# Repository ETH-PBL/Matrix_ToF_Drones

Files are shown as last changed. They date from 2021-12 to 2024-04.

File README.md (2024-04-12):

<!--
*** Template source: https://github.com/othneildrew/Best-README-Template/blob/master/README.md
-->

<!-- PROJECT SHIELDS -->
<!--
*** I'm using markdown "reference style" links for readability.
*** Reference links are enclosed in brackets [ ] instead of parentheses ( ).
*** See the bottom of this document for the declaration of the reference variables
*** for contributors-url, forks-url, etc. This is an optional, concise syntax you may use.
*** https://www.markdownguide.org/basic-syntax/#reference-style-links
-->
[][contributors-url]
[][forks-url]
[][stars-url]
[][issues-url]
[][license-url]

<!-- PROJECT LOGO -->
<br />
<p align="center">
  <a href="https://youtu.be/FyipTqjBGuM">
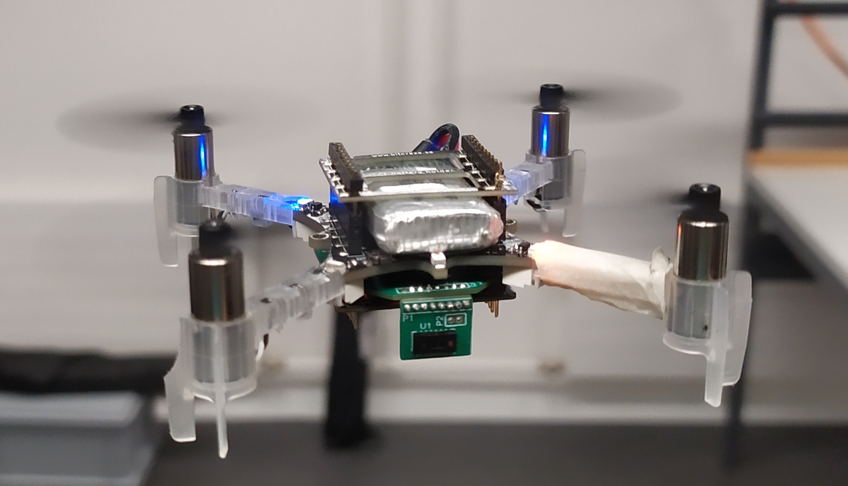
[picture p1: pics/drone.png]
    
  </a>

  <h3 align="center">Matrix_ToF_Drones</h3>

  <p align="center">
    Indoor Navigation System Based on Multi-Pixel Time-of-Flight Imaging for Nano-Drone Applications
    <br />
    <a href="https://github.com/ETH-PBL/Matrix_ToF_Drones"><strong>Explore the docs »</strong></a>
    <br />
    <br />
    <a href="https://youtu.be/FyipTqjBGuM">View Demo</a>
    ·
    <a href="https://github.com/ETH-PBL/Matrix_ToF_Drones/issues">Report Bug</a>
    ·
    <a href="https://github.com/ETH-PBL/Matrix_ToF_Drones/issues">Request Feature</a>
  </p>
</p>

<!-- TABLE OF CONTENTS -->
## Table of Contents

* [About the Project](#about-the-project)
* [Hardware](#hardware)
  * [Components](#hardware)
  * [PCB](#pcb) 
* [Dataset](#dataset)
  * [Dataset Visualizer](#visualizer)
* [Getting Started](#getting-started)
  * [Software](#software)

<!-- ABOUT THE PROJECT -->
## About The Project

Unmanned aerial vehicles (UAVs) have recently attracted the industry's attention due to their numerous civilian and potential commercial applications.
A promising UAV sub-class includes nano and micro UAVs, characterized by centimeter size, few grams of payload and extremely limited on-board computational resources. 
Those features pose major challenges to enable autonomous navigation or even more basic relevant sub-tasks, such as reliable obstacle avoidance. This project exploits a multi-zone Time of Flight (ToF) sensor to enable autonomous navigation and obstacle avoidance with a low lower computational load than most common visual-based solutions. 

### Videos and Demos
* [PBL Event: catch me if you can][video1_url]
* [Towards Reliable Obstacle Avoidance for Nano-UAVs][video2_url]
* [Enabling Obstacle Avoidance for Nano-UAVs with a multi-zone depth sensor and a model-free policy][video3_url]

## Hardware

The matrix ToF sensor, and thus this project aims to characterize and in-field evaluate the sensors <a href="https://www.st.com/resource/en/datasheet/vl53l5cx.pdf">VL53L5CX</a> from STMicroelectronics using a nano-drone platform. This project exploits a commercial nano-UAV platform, the Crazyflie 2.1 from bitcraze, together with a custom PCB designed to support two 8x8 ToF sensors. The following sections describe in detail the overall framework and the hardware setup.

### Components
The <a href="https://www.st.com/resource/en/datasheet/vl53l5cx.pdf">VL53L5CX</a> is a ToF multizone ranging sensor produced by STMicroelectronics. 
It integrates a single-photon avalanche diode (SPAD) array, physical infrared filters, and diffractive optical elements (DOE) to achieve a millimeter accuracy in various ambient lighting conditions with a wide range of cover glass materials. The working range spans between 2 cm and 4 meters, but above 2 m, the overall ranging precision degrades to 11% of the absolute distance. The most important feature of the VL53L5CX is the multizone capability, which can be configured as an 8x8 or 4x4 matrix. 
Listed below is the list of key components for our integrated deck targetted for the Crazyflie 2.1 platform: 

* [VL53L5CX][VL53L5CX_url],       ToF multizone ranging sensor
* [TPS62233][tps62233_url],       3-MHz Ultra Small Step-Down Converter
* [TCA6408A][tca6408a_url],       Low-Voltage 8-Bit I2C and SMBus I/O Expander

### PCB 
The matrix ToF printed circuit board (PCB) is built of 2 Layers with a total board thickness of only 0.43mm. Further information about the PCB can be found here:

File                                  | Content
--------------------------------------|--------
[Deck_schematics.pdf]                 | Schematics of the deck that supports 2 VL53L5CX.  
[Deck_PCB_3D.pdf]                     | Layout 3D view with details of components and nets.
[Deck_BOM.xlsx]			      | Bill of material for the Deck PCB.
[Sensor_Board_schematics.pdf]         | Schematic of the lateral PCB that holds one VL53L5CX.
[Sensor_Board_PCB_3D.pdf]             | Layout 3D view with details of components and nets.
[Sensor_Board_BOM.xlsx]               | Bill of material for the sensor board.
[Final_Assembly_3D.pdf]               | Assembly of one Deck PCB with two sensor board PCBs, front-facing and back-facing directions. 

The preview of the assembly, with details of logical connections, can be found here:

<p align="center">
<a href="https://github.com/ETH-PBL/Matrix_ToF_Drones/Hardware/TofDeck/Deck_3D.pdf">
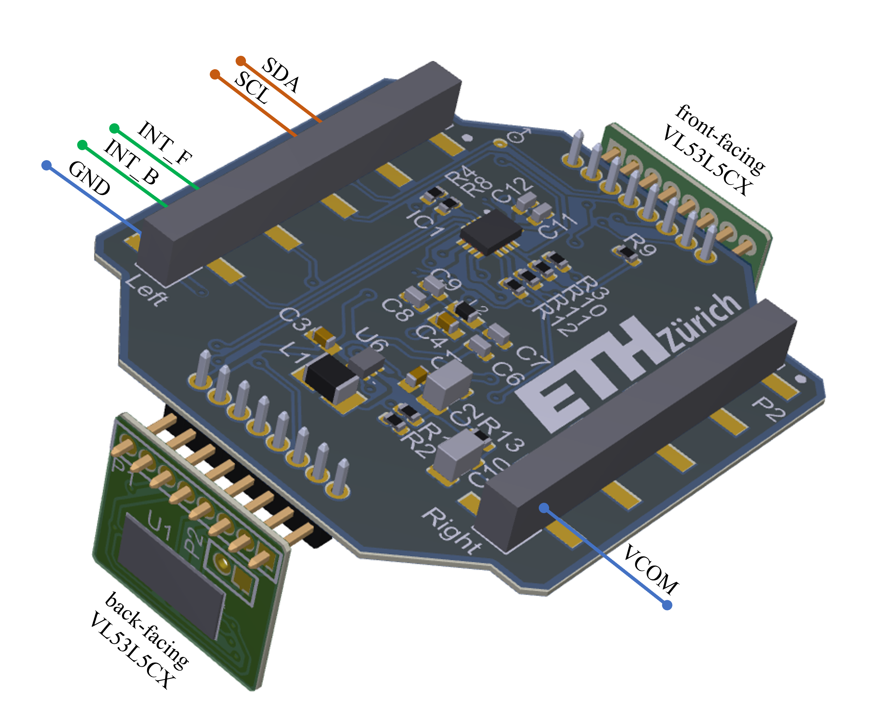
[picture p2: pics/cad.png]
    
</a>
</p>

## Dataset

Tests were performed in controlled and open spaces, with the support of a motion capture system (mocap) Vicon Vero 2.2 at a rate of 50 Hz. A human pilot manually steered the Crazyflie. Initially, the dataset was used to develop and test the obstacle avoidance algorithm. However, other researchers can also use it to improve our system by integrating the multi-zone ToF data with processed information from a CNN and the grayscale camera or by applying a more general DNN algorithm to enhance on-board intelligence. 
We collected (a) internal state estimation (attitude, velocity, position) of the Crazyflie, (b) multi-zone ToF array in 8x8 pixel configuration, (c) camera images (QVGA greyscale), (d) Vicon data (attitude, position) in a time series format with millisecond accuracy. The dataset consists of three main groups: object approach moving the drone on a single axis, yaw rotations around the Z-axis, and a general-purpose set of flying tests approaching various obstacles and narrow holes. The first group, named Linear Movements, consists of 10 recordings of flights with (a), (b), (c), and (d) data, approaching a wood panel at different speeds and stopping and flying back always on the same axis, rotations and altitude variations are disabled. The total test time is 216 seconds with an average of 22 seconds per acquisition. The next group, Yaw Rotations, consists of 3 recordings with (a), (b), (c), and (d) data, rotating on a single axis (yaw) at 1 meter from an obstacle. Recorded data reach a total of 94 seconds. The third and final group, named Obstacle Avoidance, is composed of 30 recordings with a mixed combination of (a), (b), (c), (d) - 14 acquisitions - and (a), (b), (c) - 16 acquisitions. In total, for the third group, 17 minutes of flight maneuvers are present in the Flight DataSet folder, with an average of 35 seconds per acquisition. 

The list of experiments is available here: [Flight_description.xlsx]

### Dataset Visualizer

A Conda virtual environment is provided to execute the <a href="https://github.com/ETH-PBL/Matrix_ToF_Drones/blob/main/Flight%20DataSet/Flight_visualizer.py">Flight_visualizer.py</a> script, an example of the exported video is provided below. The <a href="https://github.com/ETH-PBL/Matrix_ToF_Drones/blob/main/Flight%20DataSet/Flight_visualizer.py">Flight_visualizer.py</a> also emulate the control policy of the Crazyflie 2.1 providing the decision taken based on the input pair from the balck and white camera and the ToF sensor. Note that there are slight differences in the python and c code results - the python code does not implement a take-off phase, so the decisions while taking off do not reflect the drone's behavior (the drone first takes off to the set target height no matter the environment, as it can not fly extremely close to the ground).

```
conda env create -f environment.yml
```

then activate the environment using

```
conda activate Matrix_ToF_Drones
```

then run 

```
python Flight_visualizer.py
```

The generated videos will be saved to the folder VisualizerResults in the following format:

<p align="center">
<a href="https://github.com/ETH-PBL/Matrix_ToF_Drones">
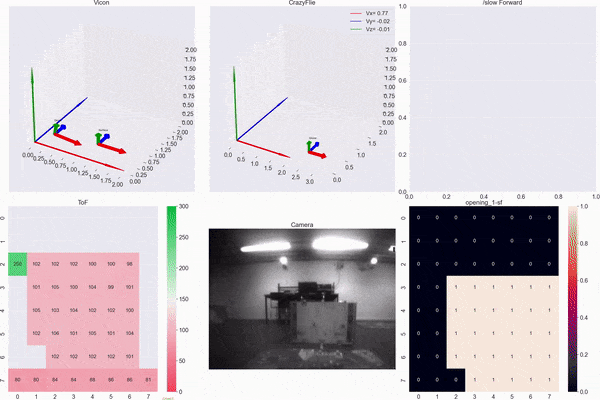
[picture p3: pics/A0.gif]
    
</a>
</p>

NOTE: The <a href="https://github.com/ETH-PBL/Matrix_ToF_Drones/blob/main/Flight%20DataSet/Flight_visualizer.py">Flight_visualizer.py</a> will export by default all the experiments from the selected folder, resulted videos will be saved to a different folder. The default settings for the source and destination folders are as below:

```
folder_address = "Approach/"
```
```
address2save = "VisualizerResults/"
```

## Getting Started

#### Material

* One fully mounted [Deck_schematics.pdf] and two [Sensor_Board_schematics.pdf] assembled as shown here: [Final_Assembly_3D.pdf]
* The [Crazyflie 2.1][crazyflie_url]
* The [Flow Deck v2][flowdeck_url]. The VL53L1x ToF sensor measures the distance to the ground with high precision and the PMW3901 optical flow sensor measures movements of the ground.

#### Software

* [Crazyflie Client][cfclient_url]
* [Altium][altium_url] (only needed for modifying the hardware)

### Building and Flashing

This work was tested using the [Crazyflie Firmware][cffw_url] at commit b0c72f2a4cb8b432211a2fa38d97c5a1dcef07ff. The code that was used for the paper titled "Robust and Efficient Depth-based Obstacle Avoidance for Autonomous Miniaturized UAVs" is found at the GitHub <a href="https://github.com/ETH-PBL/Matrix_ToF_Drones/releases/tag/v1.0">tag v1.0</a> in this repository. However, since then, the build system of the Crazyflie firmware has been updated, so to make this code compatible with newer versions the newest code in this git repo is updated to the kbuild system.

- Follow the [Crazyflie guide][cfbf_url] for building and flashing, and make sure you can compile the crazyflie-firmware without any issues
- Clone this repository and update ```CRAZYFLIE_BASE``` in the **Makefile** (in the Firmware directory) to point to your own crazyflie-firmare repository
- Open a terminal inside the Firmware folder
- Put your drone in bootloader mode
- Execute the following commands:

```
make clean
make 
make cload
```

### Take-off!

- Turn on the drone  
- Connect to it via [Crazyflie Client][cfclient_url]
- Optional: Adapt params like max vel, height, etc., if wanted (in the Parameters tab, ToF_FLY_PARAMS)
- Enter a number (in seconds) for how long it should fly (it will anyway land once the battery runs out) in the ToFly parameter
- Press enter; it will take off and start flying around!
- Optional: Look at the cmds in the Plotter tab (add a config under "Settings" "logging configurations")

## Acknowledges

If you use **Matrix ToF Drone** in an academic or industrial context, please cite the following publications:

~~~~
@article{muller2023robust,
  title={Robust and efficient depth-based obstacle avoidance for autonomous miniaturized uavs},
  author={M{\"u}ller, Hanna and Niculescu, Vlad and Polonelli, Tommaso and Magno, Michele and Benini, Luca},
  journal={IEEE Transactions on Robotics},
  year={2023},
  publisher={IEEE}
}
~~~~
~~~~
@INPROCEEDINGS{20.500.11850/476189,
	copyright = {Creative Commons Attribution 4.0 International},
	year = {2022},
	author = {Niculescu Vlad, Müller Hanna, Ostovar Iman, Polonelli Tommaso, Magno Michele, Benini Luca},
	keywords = {UAV, nano-drone, autonomous navigation, obstacle avoidance, Time of Flight},
	language = {en},
	title = {Towards a Multi-Pixel Time-of-Flight Indoor Navigation System for Nano-Drone Applications.},
}
~~~~

~~~~
@inproceedings{ostovar2022demo,
  title={Demo Abstract: Towards Reliable Obstacle Avoidance for Nano-UAVs},
  author={Ostovar, Iman and Niculescu, Vlad and M{\"u}ller, Hanna and Polonelli, Tommaso and Magno, Michele and Benini, Luca},
  booktitle={2022 21st ACM/IEEE International Conference on Information Processing in Sensor Networks (IPSN)},
  pages={501--502},
  year={2022},
  organization={IEEE}
}
~~~~

<!-- MARKDOWN LINKS & IMAGES -->
<!-- https://www.markdownguide.org/basic-syntax/#reference-style-links -->

<!--Subsection Hardware-->
[VL53L5CX_url]:     https://www.st.com/resource/en/datasheet/vl53l5cx.pdf
[tps62233_url]:     https://www.ti.com/lit/ds/symlink/tps62230.pdf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
[tca6408a_url]:     https://www.ti.com/lit/ds/symlink/tca6408a.pdf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
[crazyflie_url]:    https://www.bitcraze.io/products/crazyflie-2-1/
[flowdeck_url]:     https://store.bitcraze.io/collections/decks/products/flow-deck-v2

<!--Subsection PCB-->
[Deck_schematics.pdf]:                    /Hardware/TofDeck/TofDeck.pdf
[Deck_PCB_3D.pdf]:                        /Hardware/TofDeck/Deck_3D.pdf
[Deck_BOM.xlsx]:                          /Hardware/TofDeck/BOM_TofDeck.xlsx
[Sensor_Board_schematics.pdf]:            /Hardware/SensorBoard/SensorBoard.pdf
[Sensor_Board_PCB_3D.pdf]:                /Hardware/SensorBoard/SensorPCB_3D.pdf
[Sensor_Board_BOM.xlsx]:                  /Hardware/SensorBoard/BOM_SensorBoard.xlsx
[Final_Assembly_3D.pdf]:                  /Hardware/MultiBoard_Project/Assembly_3D.pdf

<!--Subsection Dataset-->
[Flight_description.xlsx]:	          /Flight%20DataSet/Flight%20Dataset%20Description.xlsx

[stmcubeIDE_url]:	                  https://www.st.com/en/development-tools/stm32cubeide.html
[cfclient_url]:	                          https://www.bitcraze.io/documentation/repository/crazyflie-clients-python/master/
[cffw_url]:	                          https://github.com/bitcraze/crazyflie-firmware
[cfbf_url]:	                          https://www.bitcraze.io/documentation/repository/crazyflie-firmware/master/building-and-flashing/build/
[altium_url]:	                          https://www.altium.com/
[video1_url]:	                          https://youtu.be/FyipTqjBGuM
[video2_url]:	                          https://youtu.be/m9-spY1ruAQ
[video3_url]:	                          https://youtu.be/eR2RfNcEVSU

[contributors-shield]: https://img.shields.io/github/contributors/ETH-PBL/Matrix_ToF_Drones.svg?style=flat-square
[contributors-url]: https://github.com/ETH-PBL/Matrix_ToF_Drones/graphs/contributors
[forks-shield]: https://img.shields.io/github/forks/ETH-PBL/Matrix_ToF_Drones.svg?style=flat-square
[forks-url]: https://github.com/ETH-PBL/Matrix_ToF_Drones/network/members
[stars-shield]: https://img.shields.io/github/stars/ETH-PBL/Matrix_ToF_Drones.svg?style=flat-square
[stars-url]: https://github.com/ETH-PBL/Matrix_ToF_Drones/stargazers
[issues-shield]: https://img.shields.io/github/issues/ETH-PBL/Matrix_ToF_Drones.svg?style=flat-square
[issues-url]: https://github.com/ETH-PBL/Matrix_ToF_Drones/issues
[license-shield]: https://img.shields.io/github/license/ETH-PBL/Matrix_ToF_Drones.svg?style=flat-square
[license-url]: https://github.com/ETH-PBL/Matrix_ToF_Drones/blob/master/LICENSE
[product-screenshot]: pics/drone.png

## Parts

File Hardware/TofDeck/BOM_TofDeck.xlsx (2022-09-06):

Comment | Description | Designator | Value | Manufacturer Number | Quantity | Voltage Rating
https://www.mouser.ch/ProductDetail/Kyocera-AVX/04026D475KAT2A?qs=NnBbvHfz1MlsASN%2FEU18Fg%3D%3D | Chip Capacitor, 4.7 uF, +/- 10%, 6.3 V, 0402 | C1, C3, C4 | 4.7µF | 04026D475KAT2A | 3 | 6.3V
https://www.mouser.ch/ProductDetail/Kyocera-AVX/08056D107MAT2A | Chip Capacitor, 100µF +/-20%, 6.3V, 0805, Thickness 1.45 mm | C2, C5, C10 | 100µF | 08056D107MAT2A | 3 | 6.3V
https://www.mouser.ch/ProductDetail/Kyocera-AVX/04025C102JAT2A?qs=A%252BjgVRj0cIhSqwAr58%2FhLg%3D%3D | Chip Capacitor, 1nF +/-20%, 25V, 0402, Thickness 0.6 mm | C6 | 1nF | 04025C102JAT2A | 1 | 25V
https://www.mouser.ch/ProductDetail/Kyocera-AVX/04025C104KAT4A | Chip Capacitor, 100nF +/-20%, 25V, 0402, Thickness 0.6 mm | C7, C9, C11, C12 | 100nF | 04025C104KAT4A | 4 | 25V
https://www.mouser.ch/ProductDetail/Kyocera-AVX/04025C103JAT2A | Chip Capacitor, 10nF +/-20%, 25V, 0402, Thickness 0.6 mm | C8 | 10nF | 04025C103JAT2A | 1 | 25V
https://www.mouser.ch/ProductDetail/Vishay-Semiconductors/TLMS1100-GS08?qs=%2Fjqivxn91cclYg3jNxrnHQ%3D%3D | Red Led, 20mA, 2.1 V, -40 to 100 degC, 2-Pin SMD (0603), RoHS, Tape and Reel | DS1 |  | TLMS1100-GS08 | 1
https://www.mouser.ch/ProductDetail/Vishay-Semiconductors/TLMS1100-GS08?qs=%2Fjqivxn91cclYg3jNxrnHQ%3D%3D | Red Led, 20mA, 2.1 V, -40 to 100 degC, 2-Pin SMD (0603), RoHS, Tape and Reel | DS2 |  | TLMS1100-GS08 | 1
https://www.mouser.ch/ProductDetail/Vishay-Semiconductors/TLMS1100-GS08?qs=%2Fjqivxn91cclYg3jNxrnHQ%3D%3D | Red Led, 20mA, 2.1 V, -40 to 100 degC, 2-Pin SMD (0603), RoHS, Tape and Reel | DS3 |  | TLMS1100-GS08 | 1
https://www.mouser.ch/ProductDetail/Texas-Instruments/TCA6408ARSVR?qs=AFkNxQkJKAISZm6jGsM%252BSQ%3D%3D | I/O Lo-Vltg 8B I2C & SMBus I/O Expander | IC1 |  | TCA6408ARSVR | 1
https://www.mouser.ch/ProductDetail/Murata-Electronics/LQM21PH1R0NGCD?qs=17u8i%2FzlE8%252BENrjyNDhWgQ%3D%3D | 1.0uH 1A | L1 |  | LQM21PH1R0NGCD | 1
https://www.mouser.ch/ProductDetail/Murata-Electronics/LQP15MN3N6B02D?qs=mnrSFwtzwSrVBJJUQqij4A%3D%3D | Inductor 3.6nH, 500 MHz, 500 mA, 5 Ohm, -40 to 85 degC, 0402 | L2 |  | LQP15MN3N6B02D | 1
https://www.mouser.ch/ProductDetail/Vishay-Dale/CRCW040247K5FKEDC?qs=E3Y5ESvWgWM2%2F3bSWrhiDg%3D%3D | Chip Resistor, 47,5 kOhms, +/-1 %, 63 mW, -55 to 155 degC, 0402 | R1, R3, R4 | 47.5k | CRCW040247K5FKEDC | 6
https://www.mouser.ch/ProductDetail/Panasonic/ERJ-2RKF1000X | Chip Resistor, 100 Ohms, +/-1 %, 100 mW, -55 to 155 degC, 0402 | R5, R6, R7 | 100 | ERJ-2RKF1000X | 6
https://www.mouser.ch/ProductDetail/Texas-Instruments/TPS62233DRYR?qs=DS7Z8uEdLNygkrwl%252BL3fJA%3D%3D | Buck Step Down Regulator with 2.05 to 6 V Input and 3 V Output, -40 to 85 degC, 6-Pin SON (DRY), Green (RoHS & no Sb/Br) | U6 |  | TPS62233DRYR | 1
 |  | R2,R8,R11,R12 | DNP |  | 4
Left | Header, 10-Pin | P1 | DNP | PCBComponent_1 | 1
Right | Header, 10-Pin | P2 | DNP | PCBComponent_1 | 1
Sensor_F | Header, 8-Pin | P3 | DNP | MHDR1X8 | 1
Sensor_B | Header, 8-Pin | P4 | DNP | MHDR1X8 | 1
Jumper 0402 | Jumper 0402, Current sensing jumper OR Fuse | R9, R10, R13 | 0 | RESC0402(1005)_L | 3

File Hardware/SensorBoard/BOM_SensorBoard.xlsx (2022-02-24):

Description | Designator | Footprint | Value | Quantity | Comment | Voltage Rating
Chip Capacitor, 1 uF, +/- 10%, 6.3 V, 1005 (0402 Metric) | C1, C2 | CAPC1005X55X25ML5T10 | 4.7µF | 2 | Capacitor 1 uF +/- 10% 6.3 V 1005 | 6.3V
Chip Capacitor, 100nF +/-20%, 25V, 0402, Thickness 0.6 mm | C3 | CAPC0402(1005)60_L | 100nF | 1 | Capacitor 100nF +/-20% 25V 0402 | 25V
Header, 8-Pin | P1 | MHDR1X8 |  | 1 | Sensor
Header, 2-Pin | P2 | MHDR1X2 |  | 1 | Extra IOs
Chip Resistor, 47,5 kOhms, +/-1 %, 63 mW, -55 to 155 degC, 0402 | R1, R2, R3, R4 | RESC0402(1005)_L | 47k | 4 | Resistor 47K5 +/-1 % 0402 63 mW
No Description Available | U1 | ARRAY_53L5_STM |  | 1 | VL53L5 Forward

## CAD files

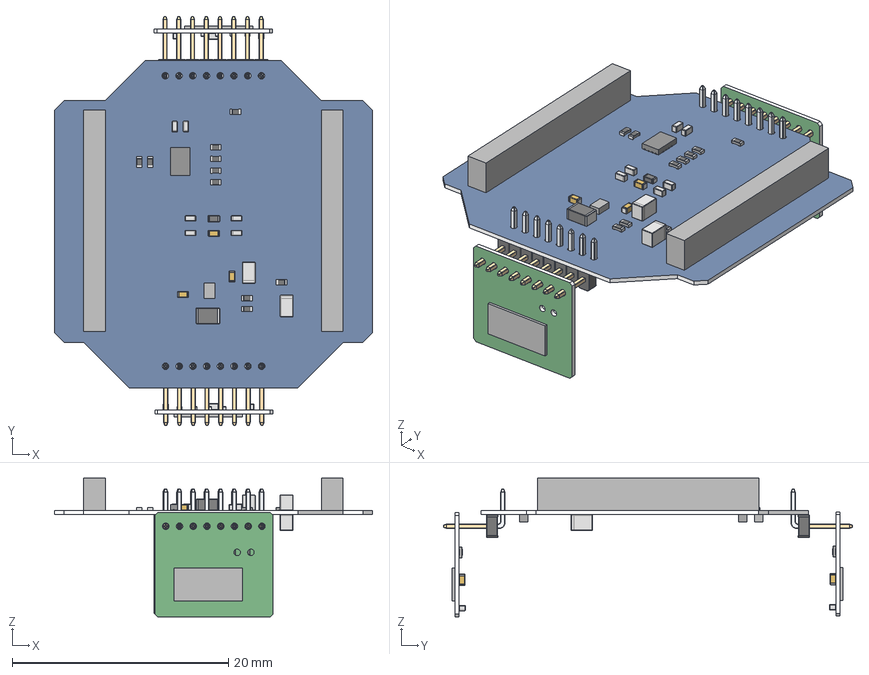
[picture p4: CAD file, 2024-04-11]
Hardware/MultiBoard_Project/Assembly.step
29.4 x 37.8 x 12.8 mm
Board x 3
U1 x 2
User Library-res0402-1 x 21
Terminal x 9
CAPC1005X60N EIA 0402(1) x 8
M50-393-Pin x 16
CAPC2012X145N EIA 0805(1) x 3
DS1
DS2
DS3
U6
BODY-SON1
FRAME-RSV0016A
P2
P1

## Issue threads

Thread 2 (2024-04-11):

Final_Assembly_3D.pdf link is a blank PDF

williamleong, 2024-04-11:
The final assembly PDF linked from the main page seems to be blank:

```
https://github.com/ETH-PBL/Matrix_ToF_Drones/blob/main/Hardware/MultiBoard_Project/Outputs/Assembly1.pdf
```

ETH-PBL, 2024-04-11:
Fixed, thanks

williamleong, 2024-04-11:
In the PCB section (https://github.com/ETH-PBL/Matrix_ToF_Drones?tab=readme-ov-file#pcb), there is a `[Final_Assembly_3D.pdf](https://github.com/ETH-PBL/Matrix_ToF_Drones/blob/main/Hardware/MultiBoard_Project/Outputs/Assembly1.pdf)` link, and in the Material section (https://github.com/ETH-PBL/Matrix_ToF_Drones?tab=readme-ov-file#material) there is the same link `[Final_Assembly_3D.pdf](https://github.com/ETH-PBL/Matrix_ToF_Drones/blob/main/Hardware/MultiBoard_Project/Outputs/Assembly1.pdf` and both now show `404 - page not found`.

I also tried to look at the commit and the file `Hardware/MultiBoard_Project/Assembly_3D.pdf` was changed, but it is also a blank PDF.

tommasopolonelli, 2024-04-12:
fixed thanks

williamleong, 2024-04-12:
Is the linked file at `https://github.com/ETH-PBL/Matrix_ToF_Drones/blob/main/Hardware/MultiBoard_Project/Assembly_3D.pdf` is meant to be a blank PDF?

tommasopolonelli, 2024-04-15:
Is not blank, you have to enable the 3D view in Adobe Reader

williamleong, 2024-04-15:
Thanks, I have done that and I am able to view it now. Appreciate your clarification.

Closed 2024-04-11.

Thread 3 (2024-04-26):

Easily Use?

Omikaa, 2024-04-26:
Hello,
If I get the Sensor Deck and ToF Deck, is it easy to use on the CF following the tutorials?
Is there any need to make some changes on the STM32？I am a little worried about the demand of professional hardware understanding.

tommasopolonelli, 2024-06-28:
Yes you need to modify the firmware to support the ToF Deck.

AZyfen, 2024-07-06:
> Hello, If I get the Sensor Deck and ToF Deck, is it easy to use on the CF following the tutorials? Is there any need to make some changes on the STM32？I am a little worried about the demand of professional hardware understanding.

Hello, have you implemented this code? How can I solve the issue of it not flying stably?

Closed 2024-06-28.

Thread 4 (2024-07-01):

Why can't it detect the flow-deck？

AZyfen, 2024-07-01:
Hello,I followed your manual and tried to deploy on the Crazyflie, but why does the Crazyflie bounce and fail to take off normally? What could be the reason?

Closed 2024-07-04.

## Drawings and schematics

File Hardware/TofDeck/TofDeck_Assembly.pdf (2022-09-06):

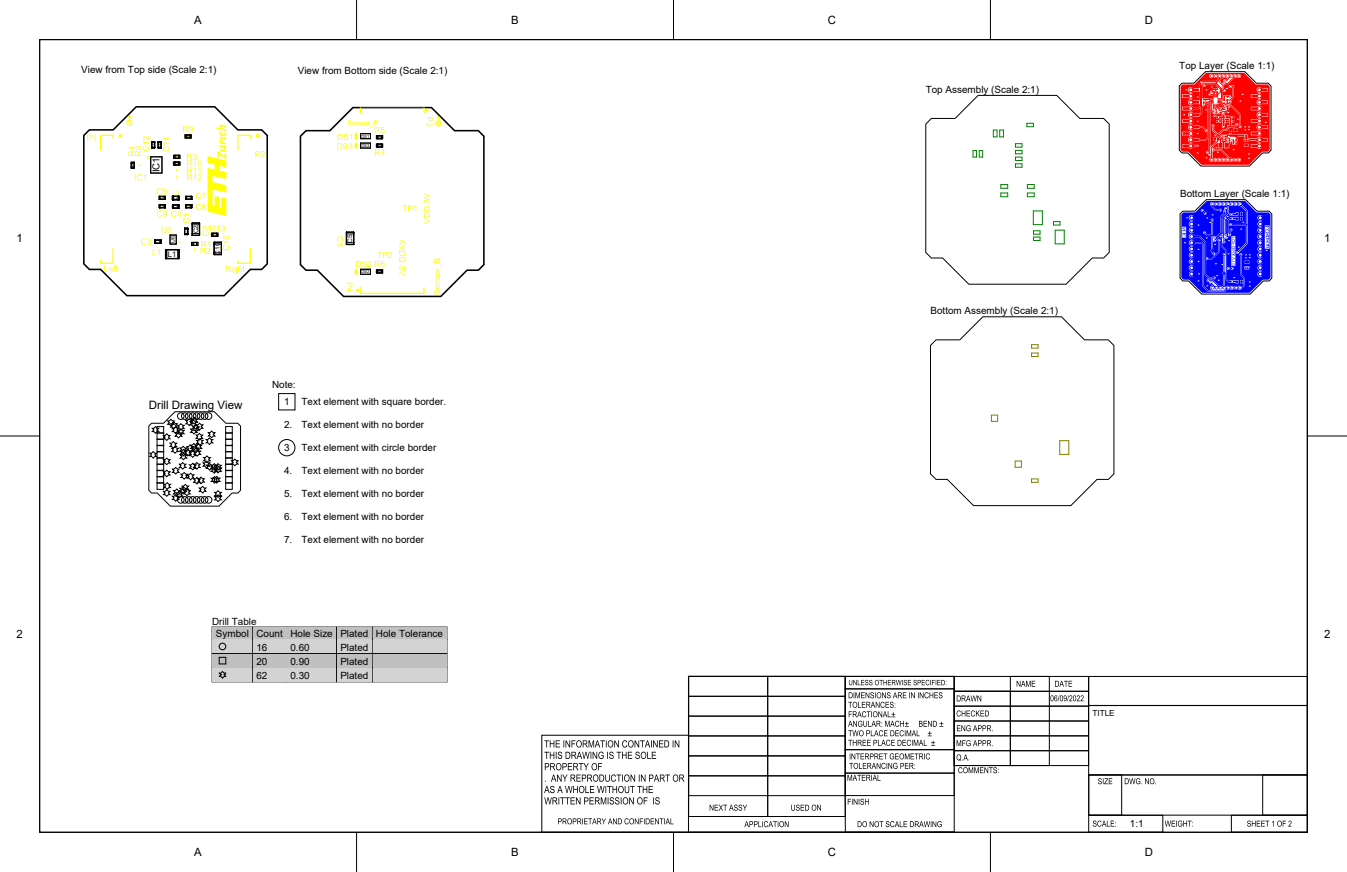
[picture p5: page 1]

View from Top side (Scale 2:1)

Note:
1 Text element with square border.

2. Text element with no border

3 Text element with circle border

4. Text element with no border

5. Text element with no border

6. Text element with no border

7. Text element with no border

Symbol | Count | Hole Size | Plated | Hole Tolerance

16 | 0.60 | Plated
20 | 0.90 | Plated
62 | 0.30 | Plated

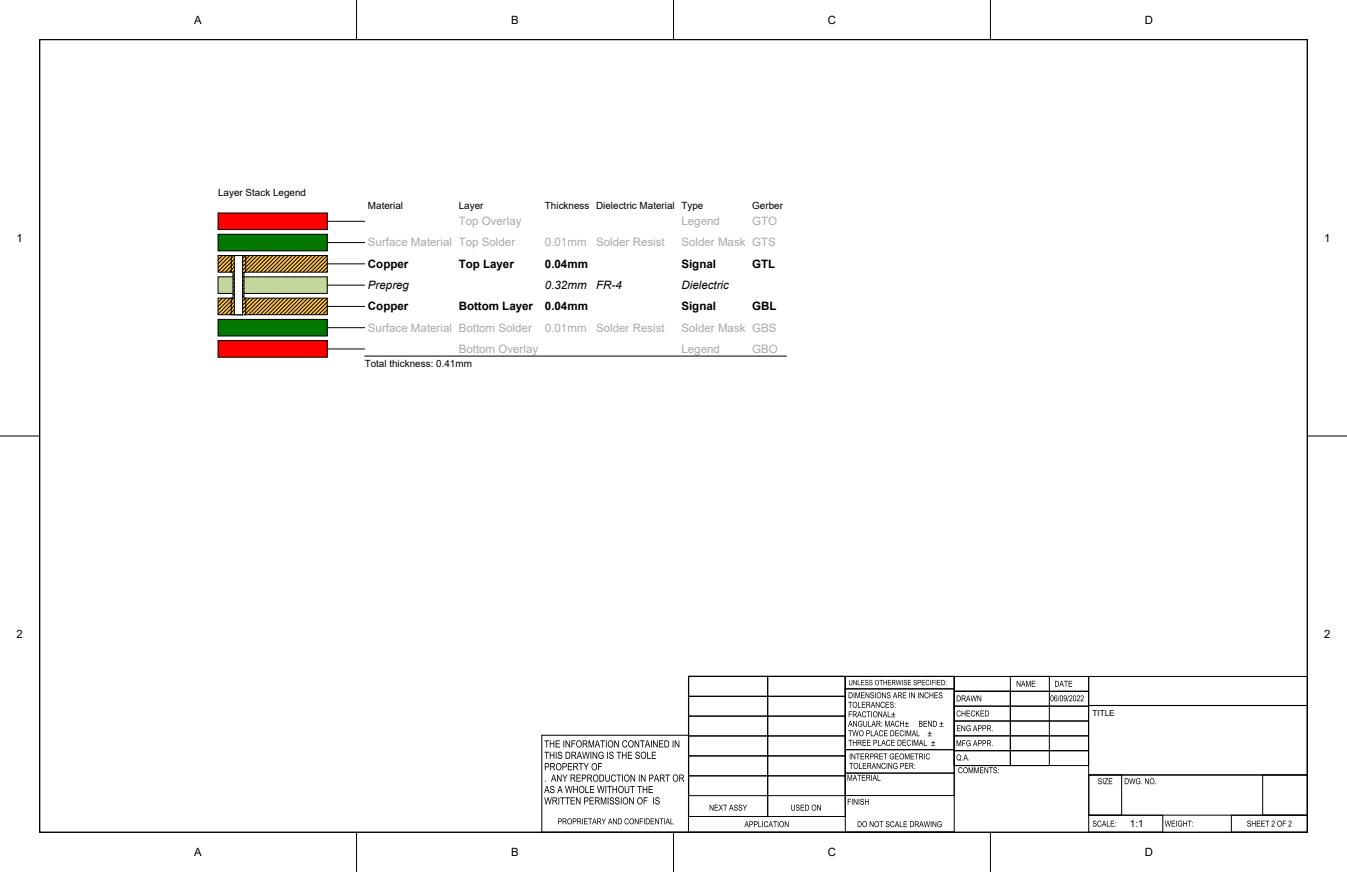
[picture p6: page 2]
Material; Layer; Thickness Dielectric Material Type; Gerber; Top Overlay; Legend; GTO; Surface Material Top Solder; 0.01mm Solder Resist; Solder Mask GTS; Copper; Top Layer; Signal; GTL; Prepreg; Dielectric; Bottom Layer 0.04mm; GBL; Surface Material Bottom Solder 0.01mm Solder Resist; Solder Mask GBS; Bottom Overlay; GBO; Total thickness: 0.41mm; TITLE

Layer Stack Legend

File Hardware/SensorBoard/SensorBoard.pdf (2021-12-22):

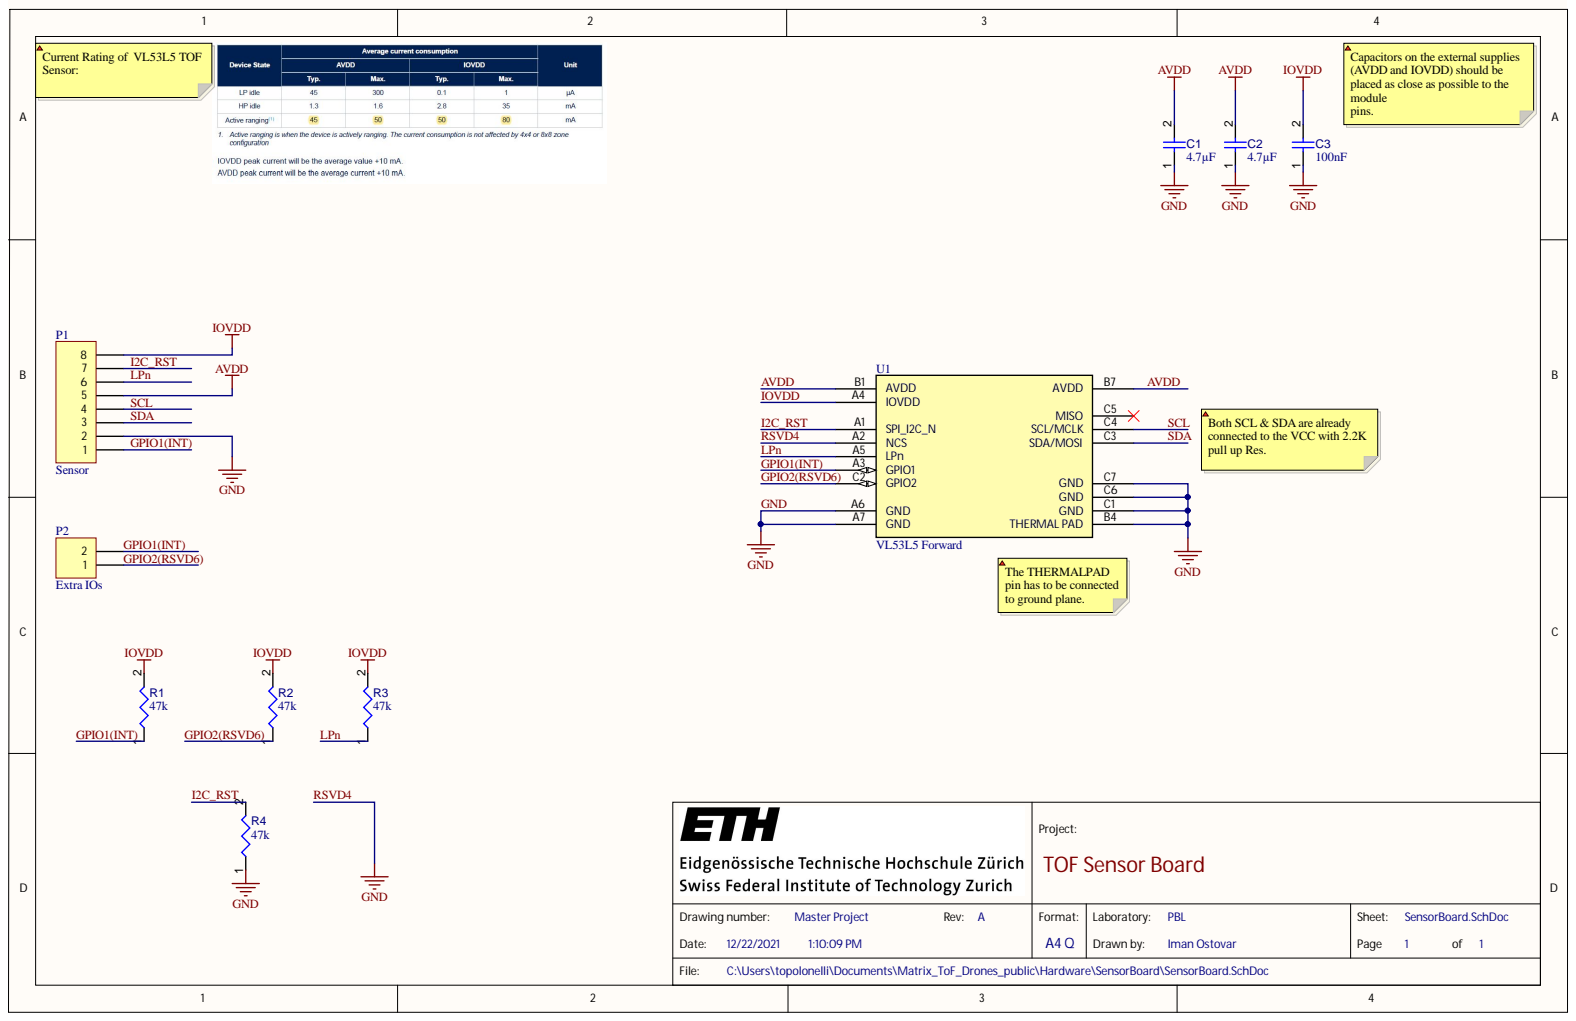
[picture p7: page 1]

rnal supplies
as possible to the

The THERMALPA
pin has to be
to ground plane

Proj ect: TOF Sensor Board

Drawi ng n umber: Master Proj ect Rev: A Date : 12/22/2021 1:1 0:0 9 PM | Format: A4 Q | Laboratory : PBL Drawn by : Iman Ostovar | S h e et: Se nsorBoard.SchDo c Page 1 o f 1

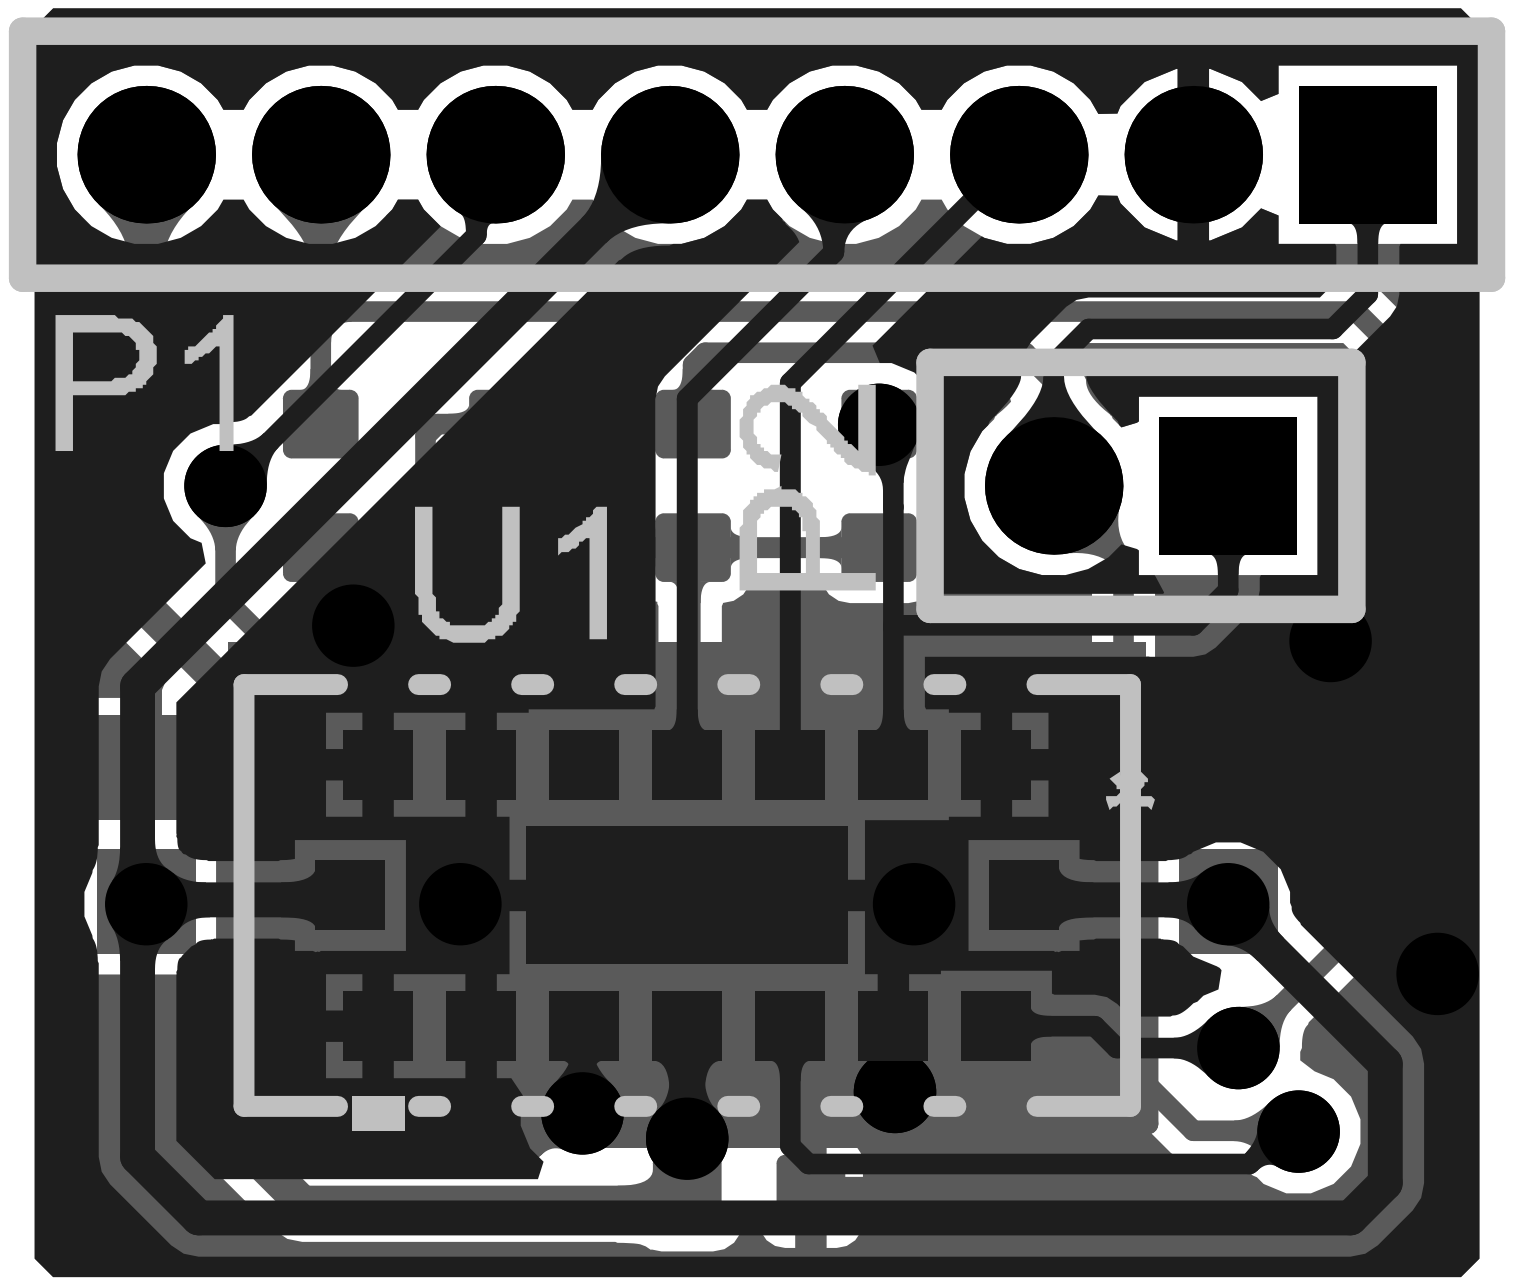
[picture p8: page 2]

Comment | Description | Designator | Footprint | LibRef | Quantity
Capacitor 1 uF +/- 10% 6.3 V 1005 Chip Capacitor, 1 uF, +/- 10%, 6.3 V, 1005 (0402 Metric) C1, C2 | | | CAPC1005X55X25ML5T10 CMP-001-00009-6 | | 2
Capacitor 100nF +/-20% 25V 0402 Chip Capacitor, 100nF +/-20%, 25V, 0402, Thickness 0.6 mm C3 | | | CAPC0402(1005)60_L CMP-001-00065-4 | | 1
Sensor | Header, 8-Pin | P1 | MHDR1X8 | MHDR1X8 | 1
Extra IOs | Header, 2-Pin | P2 | MHDR1X2 | MHDR1X2 | 1
Resistor 47K5 +/-1 % 0402 63 mW Chip Resistor, 47,5 kOhms, +/-1 %, 63 mW, -55 to 155 degC, 0402 R1, R2, R3, R4 | | | RESC0402(1005)_L | CMP-009-00137-3 | 4
VL53L5 Forward | No Description AvailableU1 | | ARRAY_53L5_STM | VL53L5 | 1

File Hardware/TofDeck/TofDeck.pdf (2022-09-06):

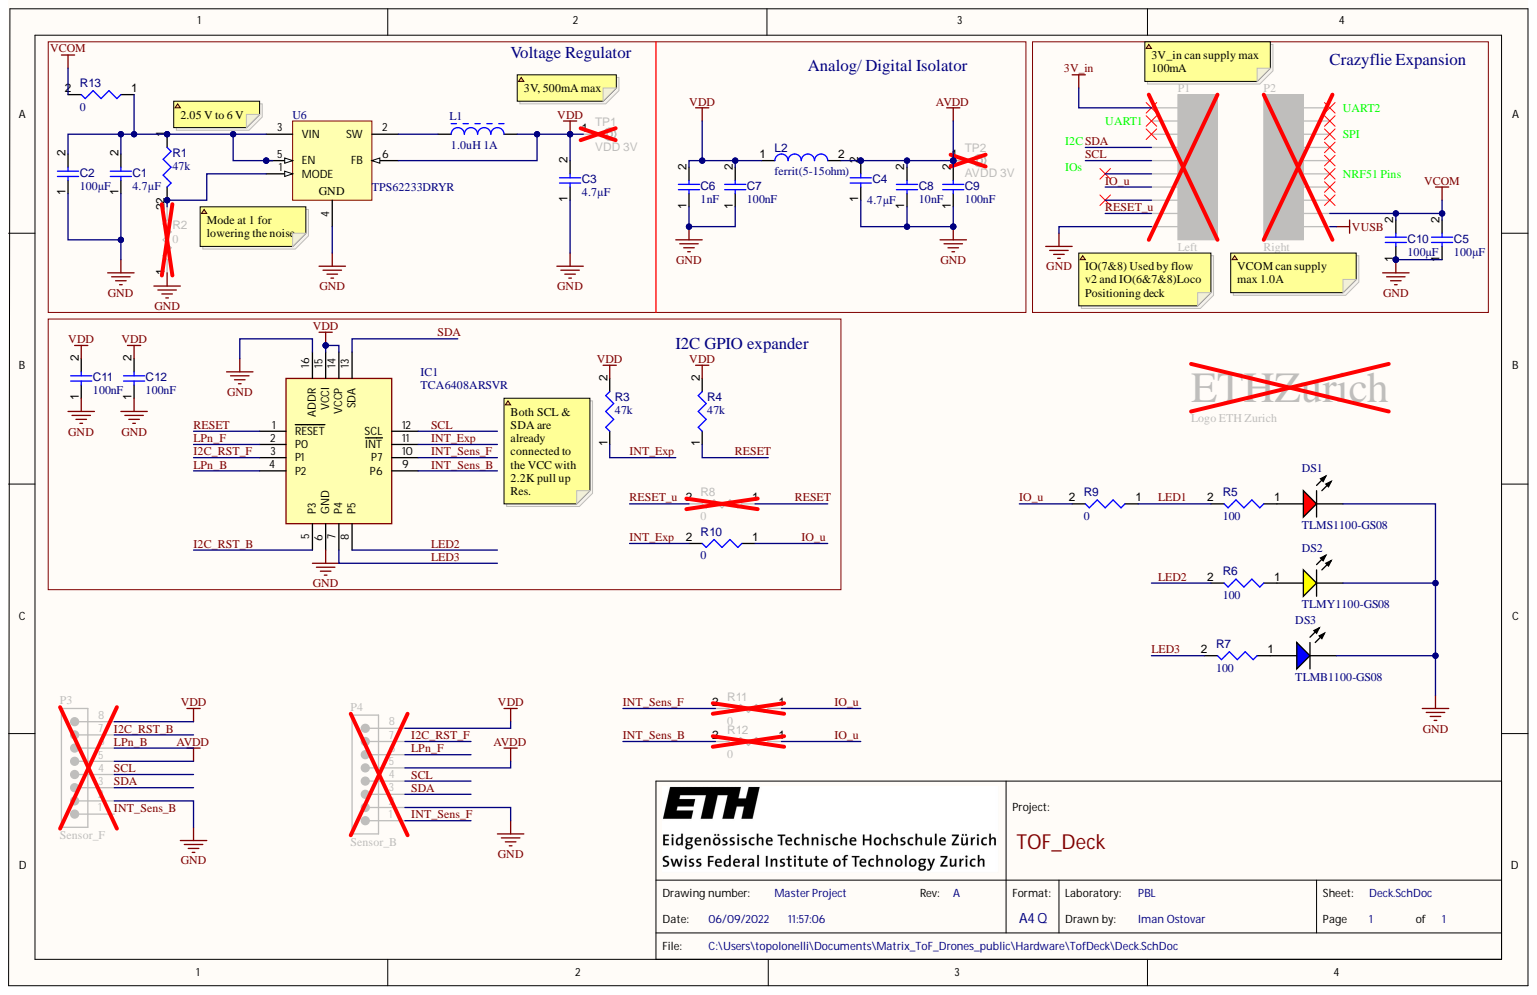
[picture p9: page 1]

IO(7&8) Used by flow
v2 and IO(6&7&8)Loco
Positioning deck

ETHZurich Logo ETH Zurich

1 | INT_Sens_B

1 | INT_Sens_F

Project: TOF_Deck

Drawing number: Master Project Rev: A Date: 06/09/2022 11:57:06 | Format: A4 Q | Laboratory: PBL Drawn by: Iman Ostovar | Sheet: Deck.SchDoc Page 1 of 1

C:\Users\topolonelli\Documents\Matrix_ToF_Drones_public\Hardware\TofDeck\Deck.SchDoc

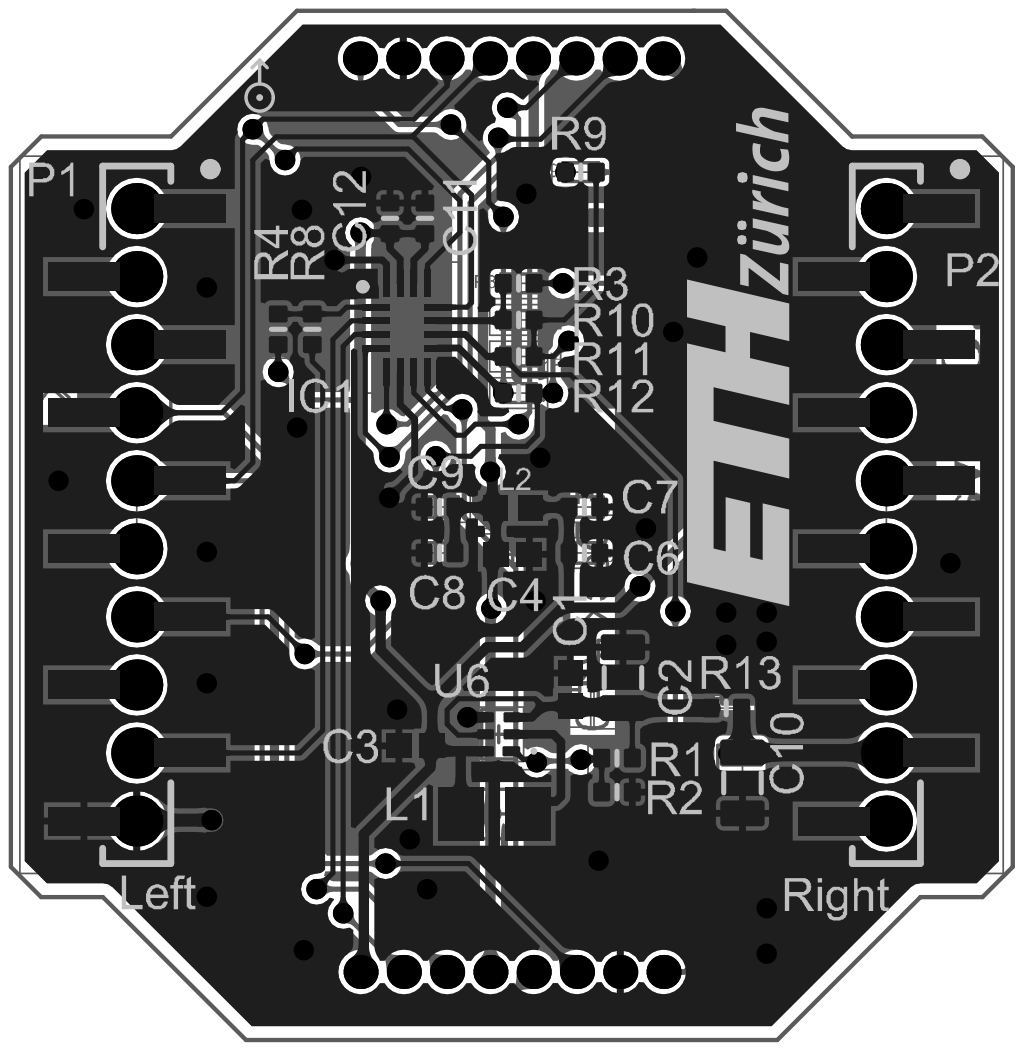
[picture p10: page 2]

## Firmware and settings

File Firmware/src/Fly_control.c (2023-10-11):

/* 
 * Copyright (C) 2023 ETH Zurich
 * All rights reserved.
 *
 * This software may be modified and distributed under the terms
 * of the GPL-3.0 license.  See the LICENSE file for details.
 *
 * Authors: Hanna Müller, Vlad Niculescu, Tommaso Polonelli, Iman Ostovar
 */

#include "system.h"
#include "FreeRTOS.h"
#include "task.h"
#include "motors.h"
#include "estimator_kalman.h"
#include "commander.h"
#include "deck.h"
#include "Fly_control.h"
#include <math.h>

#include "debug.h"
#include "log.h"
#include "param.h"
#include "pm.h"



uint32_t last_time = 0;
// static uint32_t delta_time = 0;
//flight parameters
volatile float current_height = 0.0;
//param
float MAX_VX = 1.0f;
float MAX_AX = 1.0f;
float MAX_NEG_AX = 10.0f;
float START_TAKE_OFF_HEIGHT= 0.6f;
static bool isFlying = false;
//
extern uint16_t ToFly;

static void TakeOff(float height);
static void Land(void);
static void headToSetpoint(float x, float y, float z, float yaw);
static setpoint_t CreateSetpoint(float x_vel, float y_vel, float z, float yaw_rate);
static void setHoverSetPoint(float x_vel, float y_vel, float z_vel, float yaw_rate);
static void positionSet(setpoint_t *setpoint, float x, float y, float z, float yaw);
static uint32_t get_time_stamp();

void fly_task_land()
{
    Land(); 
    isFlying = false;
}

void fly_task_take_off()
{
    isFlying = true;
    // Reset estimator
    estimatorKalmanInit();
    // Take off
    TakeOff(START_TAKE_OFF_HEIGHT);
}

bool fly_task(FlyCommand_t fly_command)
{

    //update time
    if (last_time == 0)
    {
        // delta_time = 0;
        last_time = get_time_stamp();
    }
    uint32_t delta =  get_time_stamp();
    if(
        (delta - last_time >= ToFly * MAX_FLIGHT_DURATION && isFlying == true) ||
        pmIsBatteryLow()
      )
    {
        Land();
        // DEBUG_PRINT("Landed\n"); 
        isFlying = false;
        return isFlying;
    }

    if (isFlying == false || pmIsChargerConnected())
    {
        // commanderNotifySetpointsStop(50);
        return isFlying;
    }

    float Vx = 0; 
    float Vy = 0;
    float Vz = 0;
    float yaw_rate = 0 ;

    Vx = fly_command.command_velocity_x;
    if (fly_command.command_velocity_x > 0.99f)
    {
        Vx = MAX_VX;
    }
    Vz = fly_command.command_velocity_z *  MAX_VZ;
    yaw_rate =  fly_command.command_turn * MAX_YAW_RATE;
   
    setHoverSetPoint(Vx, Vy, Vz, yaw_rate);

    return isFlying;
}


static void TakeOff(float height) {
    vTaskDelay(DELAY_TO_LAUNCH);
    point_t pos;
    memset(&pos, 0, sizeof(pos));
    estimatorKalmanGetEstimatedPos(&pos);

    uint32_t endheight = (uint32_t)(100 * (height - 0.3f));
    for(uint32_t i=0; i<endheight; i++) {
        headToSetpoint(pos.x, pos.y, 0.3f + (float)i / 100.0f, 0);
        vTaskDelay(30);
    }

    current_height = height;
    vTaskDelay(DELAY_AFTER_LAUNCH); // wait for being stablize
}

static void Land(void) {
    point_t pos;
    memset(&pos, 0, sizeof(pos));
    estimatorKalmanGetEstimatedPos(&pos);

    float height = pos.z;
    float current_yaw = logGetFloat(logGetVarId("stateEstimate", "yaw"));

    for(int i=(int)100*height; i>100*END_LANDING_HEIGHT; i--) {
        // setHoverAltitude((float)i / 100.0f);
        headToSetpoint(pos.x, pos.y, (float)i / 100.0f, current_yaw);
        vTaskDelay(40);
    }
    current_height = 0;
    vTaskDelay(300);
    motorsSetRatio(MOTOR_M1, 0);
    motorsSetRatio(MOTOR_M2, 0);
    motorsSetRatio(MOTOR_M3, 0);
    motorsSetRatio(MOTOR_M4, 0);
    vTaskDelay(200);
}


static void headToSetpoint(float x, float y, float z, float yaw)
{
    setpoint_t setpoint;
    positionSet(&setpoint, x, y, z, yaw);
    commanderSetSetpoint(&setpoint, 3);
}


static void setHoverSetPoint(float x_vel, float y_vel, float z_vel, float yaw_rate)
{
    current_height += z_vel * (75.0f/1000.0f);

    if((float)fabs(z_vel - 0.0f) < 0.01f && (float)fabs(current_height - START_TAKE_OFF_HEIGHT) > 0.05f )
    {
        if (current_height > START_TAKE_OFF_HEIGHT)
            current_height -= SLOW_VZ * TOF_PERIOD;
        else
            current_height += SLOW_VZ * TOF_PERIOD;
    }

    //control values and send 
    if (current_height < MIN_HEIGHT)
        current_height = MIN_HEIGHT;
    else if (current_height > MAX_HEIGHT)
        current_height= MAX_HEIGHT;
    
    // check for accelerations
    static float previous_vx = 0;

    if ((x_vel > previous_vx) && ((x_vel - previous_vx) > (MAX_AX*TOF_PERIOD)))
    {
        x_vel = previous_vx + (MAX_AX*TOF_PERIOD);
    }
    if ((x_vel < previous_vx) && ((previous_vx - x_vel) > (MAX_NEG_AX*TOF_PERIOD)))
    {
        x_vel = previous_vx - (MAX_NEG_AX*TOF_PERIOD);
    }
    previous_vx = x_vel ;


    setpoint_t setpoint = CreateSetpoint(x_vel, y_vel, current_height, yaw_rate);
    commanderSetSetpoint(&setpoint, 3);

}


static void positionSet(setpoint_t *setpoint, float x, float y, float z, float yaw)
{
    memset(setpoint, 0, sizeof(setpoint_t));

    setpoint->mode.x = modeAbs;
    setpoint->mode.y = modeAbs;
    setpoint->mode.z = modeAbs;

    setpoint->position.x = x;
    setpoint->position.y = y;
    setpoint->position.z = z;

    setpoint->mode.yaw = modeAbs;

    setpoint->attitude.yaw = yaw;

    setpoint->mode.roll = modeDisable;
    setpoint->mode.pitch = modeDisable;
    setpoint->mode.quat = modeDisable;
}

static setpoint_t CreateSetpoint(float x_vel, float y_vel, float z, float yaw_rate)
{
	setpoint_t setpoint;	
	memset(&setpoint, 0, sizeof(setpoint_t));
	setpoint.mode.x = modeVelocity;
	setpoint.mode.y = modeVelocity;
	setpoint.mode.z = modeAbs;
	setpoint.mode.yaw = modeVelocity;

	setpoint.velocity.x	= x_vel;
	setpoint.velocity.y	= y_vel;
	setpoint.position.z = z;
	setpoint.attitudeRate.yaw = yaw_rate;
	setpoint.velocity_body = true;
	return setpoint;
}

static uint32_t get_time_stamp()
{
  uint32_t timestamp = ((long long)xTaskGetTickCount())/portTICK_RATE_MS;
  //DEBUG_PRINT("ToFDeck timestamp: %d (size: %d)\n", timestamp,sizeof(timestamp));
  return timestamp;
}




PARAM_GROUP_START(ToF_FLY_PARAMS)
PARAM_ADD(PARAM_FLOAT, MAX_VX, &MAX_VX)
PARAM_ADD(PARAM_FLOAT, MAX_AX, &MAX_AX)
PARAM_ADD(PARAM_FLOAT, MAX_NEG_AX, &MAX_NEG_AX)
PARAM_ADD(PARAM_FLOAT, defaultH, &START_TAKE_OFF_HEIGHT)
PARAM_GROUP_STOP(ToF_FLY_PARAMS)

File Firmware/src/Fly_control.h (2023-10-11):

/* 
 * Copyright (C) 2023 ETH Zurich
 * All rights reserved.
 *
 * This software may be modified and distributed under the terms
 * of the GPL-3.0 license.  See the LICENSE file for details.
 *
 * Authors: Hanna Müller, Vlad Niculescu, Tommaso Polonelli, Iman Ostovar
 */

#ifndef FLY_CONTROL // include guard
#define FLY_CONTROL

// #include <string.h>
#include <stdint.h>
#include <stdbool.h>
// #include "deck.h"
// #include "debug.h"
// #include <string.h>
// #include <math.h>

#include "ToF_process.h"
// #include "param.h"
// #include "config_params.h"



#define COMMAND_VALID_TIME 4000

#define END_LANDING_HEIGHT 0.07f
#define MAX_HEIGHT 1.2f
#define MIN_HEIGHT 0.2f
#define MAX_YAW_RATE 60.0f

#define SLOW_VZ 0.05f
#define MAX_VZ 0.5f

#define DELAY_TO_LAUNCH 500  //ms
#define DELAY_AFTER_LAUNCH 300  //ms

#define MAX_FLIGHT_DURATION 1000 //ms

void fly_task_take_off();
void fly_task_land();
bool fly_task(FlyCommand_t command);


#endif /* FLY_CONTROL */

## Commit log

2021-12-13 add hardware degins files
    [Assembly1.step, Deck.PcbDoc, Deck.SchDoc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]
2021-12-22 PDFs and images
    [Deck.PcbDoc, SensorBoard.PrjPcb, TofDeck.PrjPcb]
2022-02-24 - update BOM
    [BOM_SensorBoard.xlsx, BOM_TofDeck.xlsx]
2022-05-16 Flight DataSet structure
    [Assembly.step, Flight Dataset Description.xlsx, SensorBoard.PrjPcb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]
2022-09-06 - BOM Update TofDeck
    [BOM_TofDeck.xlsx, Deck.PcbDoc, Deck.SchDoc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]
2023-08-29 Flight DataSet Upload
    [TofDeck.PrjPcb, state_Crazyflie_group00.csv, state_Crazyflie_group01.csv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]
2023-10-11 Gerber files for the SensorBoard.PrjPcb and TofDeck.PrjPcb
    [Deck.PcbDoc, SensorBoard.PrjPcb, TofDeck.PrjPcb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]
2024-04-11 MultiBoard_Project/Assembly.step and .pdf
    [Assembly.step, Assembly1.step]
